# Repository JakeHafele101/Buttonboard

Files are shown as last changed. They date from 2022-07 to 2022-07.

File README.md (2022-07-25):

# Buttonboard Repository

Buttonboard takes button inputs from the drivers wheel and communicates those signals to HAL over our CAN network to turn on our lights and horn.

Some say this is the best board to ever exist on the team. Some also say that the smartest people on the team have worked on this board.

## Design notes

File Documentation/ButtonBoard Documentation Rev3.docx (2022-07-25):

Buttonboard

Project (P15) | Current Rev # C | March 18, 2021 | Bryce Staver

HARdware Documentation

Prisum solar car

2021

Revision History
Rev # | Description | Hardware Manager | Approved By Need 2/3 for approval: eteam director or assistant director, eteam manager, or alumni
P14 Rev | P14 buttonboard | Bryan Kalkhoff
Rev 1 | Reworked buttonboard from P14 and simplified it a ton. This was started as a new member project Fall 2020. Most of the changes were done here. | Bryce Staver | Bryan Kalkhoff, Ashley Robertson
Rev 2 | We changed the 12V connector to a Megafit and added a reverse polarity protection. | Bryce Staver | Bryan Kalkhoff, Ashley Robertson
Rev 3 | Added input debouncing and power filtering for 12V_Main coming into the board | Bryan Kalkhoff | Douglas Zuercher, Ashley Robertson

Additional Resources……………………………………………………………………………………...9

Prisum Contacts..………………………………………………………………………………………9

Other Contacts………………………………………………………………………………………10

# Theory of Operation

## Description

Buttonboard is used to take in inputs from the driver of the car and send them to our compute module. It has one 6 pin connector to take in all these inputs, which are the core of the board. Buttonboard is powered off 12V_Main.

## Board Placement

Buttonboard is placed on the inside of the car on the driver’s side. Specifically, it is on the front panel by the steering column. Refer to Figure 1 for a diagram in how the board and inputs will fit into the car. Buttonboard’s dimensions are 4.355 inches long and 3.341 inches wide. The mounting holes are offset 5.842mm in the y direction and offset 6.35mm in the x direction. The diameter of the mounting holes is 4.445mm. The block diagram below gives a general idea of how the board will fit into the front of the car. Figure 2 below demonstrates where the board is being placed behind the wheel and under the steering column.

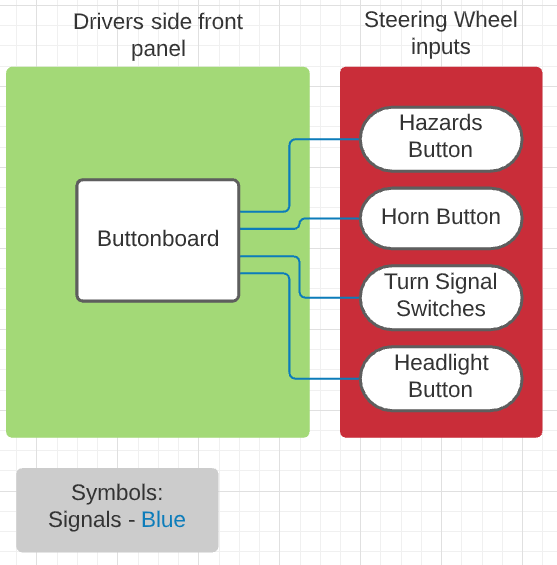
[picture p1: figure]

Figure 1. Buttonboard placement diagram

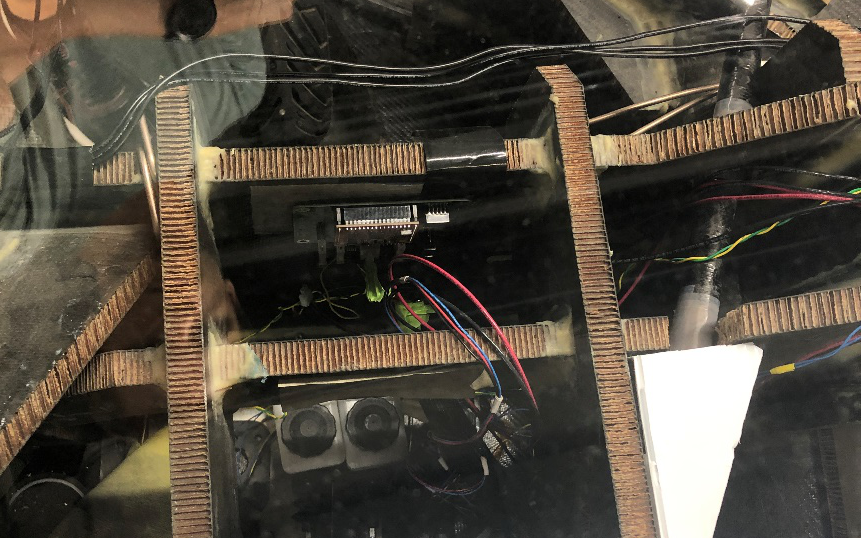
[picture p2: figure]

Figure 2. Buttonboard placement

## Purpose

the purpose of buttonboard is to provide an input driver interface for the car. The board will take in different inputs and send those signals to other boards through CAN to turn digital signals on or off for parts like our horn or turning lights.

# Application

## System Level

### Block Diagram

Buttonboard will get 12V_Main voltage from powerboard. The inputs in buttonboard will be processed through CAN and sent to front and rear HAL to turn on different signals in the car like turn lights, horn, or hazard lights. Figure 3 demonstrates a block diagram showing how buttonboard gets power from powerboard and sends its CAN signals to the front and rear HAL boards.

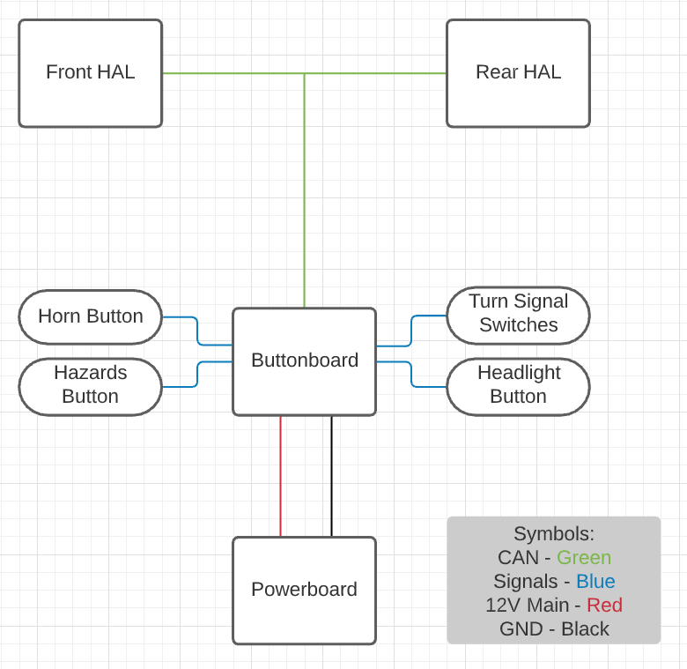
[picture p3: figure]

Figure 3. Buttonboard system diagram

### Pin Diagram

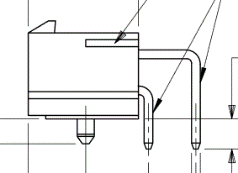
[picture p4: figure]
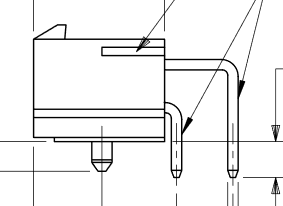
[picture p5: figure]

Figure 4. 2 pin connector diagram Figure 5. 6 pin diagram

A pin connection table is provided below for wiring purposes. In general, the wire with a greater voltage on it is connected to the lower pins, and the wire with a lower voltage on it is connected to the upper pins of a connector. The intention of wiring in this fashion is to decrease the chances of someone accidentally brushing the connector and touching the high-voltage signal.

Table 1: Pin diagram

Connector designator | Connector Type | Pin # | Description of Signal
J1 – 12V_Main | Megafit | 1 – MGND 2- 12V_Main | 12V_Main from powerboard
J2 – 5V_INPUT | Minifit | 1 – 5V 2 – MGND | 5V input possibly needed for buttons. NOT CURRENTLY USED
J3 – CAN1 | Minifit | 1 – CAN_H 2 – CAN_L | CAN1 Connector
J4 – CAN2 | Minifit | 1 – CAN_H 2 – CAN_L | CAN2 Connector
J5 – Button Inputs | Minifit | 1 – Left Turn 2 – Right Turn 3 – Horn 4 – Running Lights 5 – Hazards 6 - Brights | Takes in inputs for different buttons and switches from the driver’s side of car

To note here, right now we are not using both running lights and brights. When designing the board, we were unsure of if we would use both, so we have them labeled with different nets and inputs on connector J5. They are listed here since they are still a separate input in the schematic. It is now the case that Brights is being used now for cruise control, but that is not represented on the silkscreen on the board.

### Mounting buttons on wheels

There are 5 buttons attached on the driver’s wheel. The positive end of the buttons are wired through the J5 button input connector and the negative end of the button is wired through a chain of ground wires that go around the wheel. The buttons on the wheel are left turn, right turn, horn, hazards, and cruise control. Left turn, right turn, cruise control, and the hazards buttons are all latching. For the sake of everyone’s ears, the horn is non latching, so it will not stay pressed down after pushed.

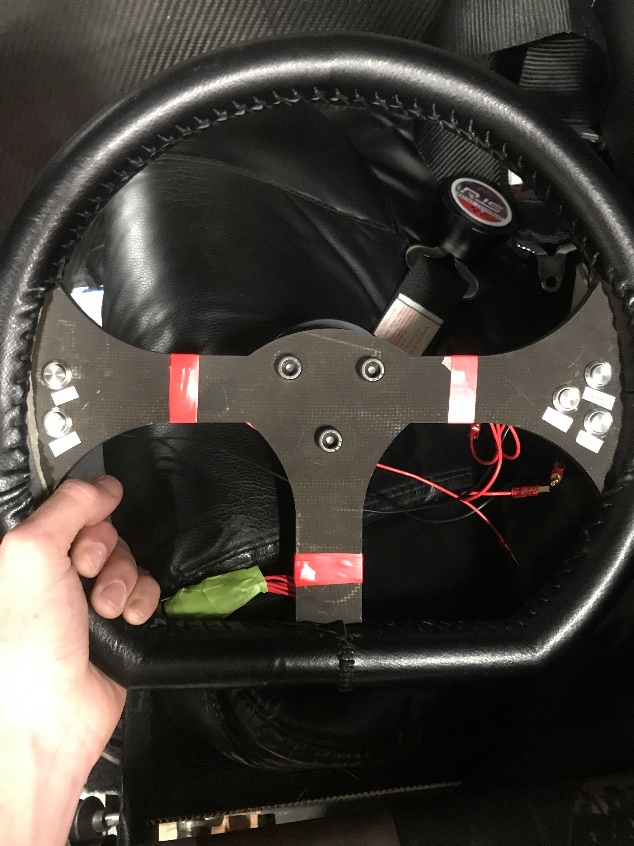
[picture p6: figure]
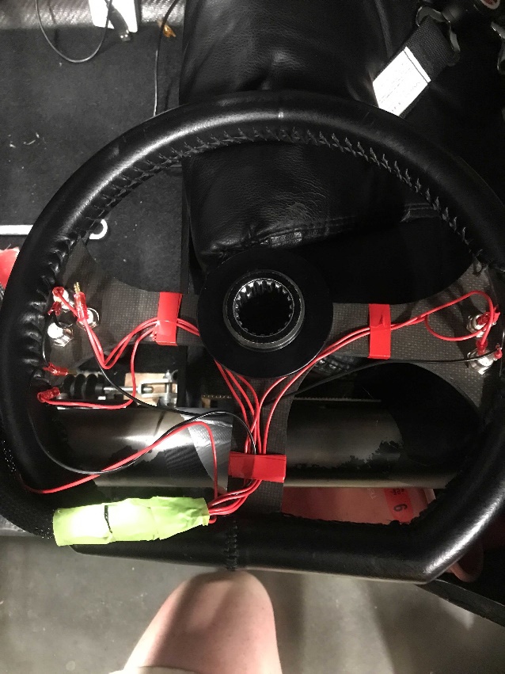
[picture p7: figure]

Figure 6. Back of wheel Figure 7. Front of wheel

## Board Level

### Schematic

Buttonboard’s schematic can be seen in Figure 10. For connectors, it should be noted that J1, the 12V_Main connector, is a megafit connector instead of a minifit, unlike the other connectors. This is something that was changed across all the boards to help us from accidentally frying compute modules.

Power

The circuitry between the 12V_Main megafit connector and the 5V switching reg, U1, is standard between a few different boards. Specifically, HAL and motorboard were designed around the same time as buttonboard and share a similar circuit and parts. The first PMOS, Q2, is used for reverse polarity protection. This is here so that just in case we accidentally swap our 12V and MGND inputs, we can’t accidentally burn anything up. Since we are using a PMOS, if our ground is connected in the right pin of the connector, pin 1, then the gate will enable the mosfet to send the 12V source from the drain (3 of Q2) to source (2 of Q2). F1 is our fuse holder. If our fuse is blown or not connected, a second PMOS (Q1) will turn on the Fault LED indicator. C1 is a decoupling capacitor that helps smooth out our input voltage into the 5V switching regulator. D1 is a TVS diode that helps to prevent fast voltage spikes to protect our circuit.

U1 is our switching regulator that turns our 12V voltage into 5V. Because of the TVS diode (D1), we had a 0.7V drop in our input, which LED us to use R1 and R3. These two resistors are used to adjust the output voltage to help us get as close to 5V as we can. Before we added these, we were getting around a 4.2 V output. After the switching regulator we have a 5V LED Indicator to show that the switching regulator is working as we need and to show that our 5V plane on top of the board has voltage on it.

The power filtering circuit, shown in Figure 8, helps us smooth high frequency noise from our 12V line coming into buttonboard. FB1 is a ferrite bead, which can be used to filter out the unwanted noise. The capacitors after it are designed to be placed in decreasing order of capacitance and size. If you look at the PCB design, you will notice that C1 and C8 have a package size of 1206, C9 has 0805, and C10 has 0603. They also decrease in order of capacitance, which is easier to see on the schematic.

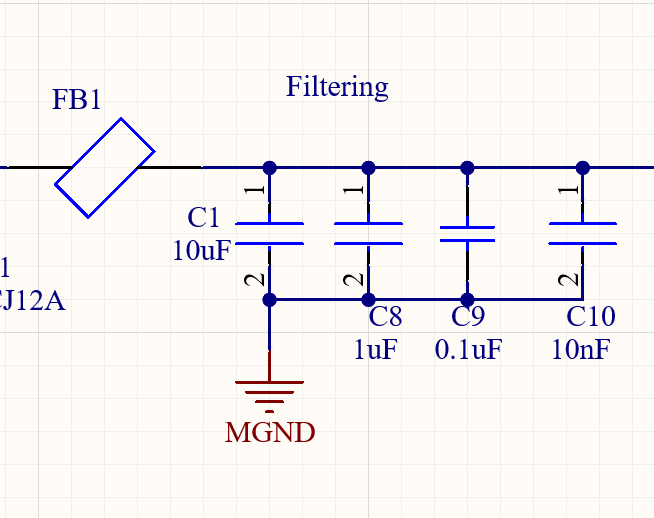
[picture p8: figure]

Figure 8. Power filtering circuit

Connectors

We have two connectors for can, which can be seen with the J3 and J4 connectors. These go into the CANH and CANL pins of the S+ (U2). For the input section, we have a 6 pin minifit connector, J5, used to get our actual button and switch inputs from the car. These inputs will then go into Port B pins of the S+.

Pullup Resistors

Each input is wired to a pullup resistor, as seen by R4 for example. This makes it so that all the inputs will default to a logic high normally. J2 as of now will not be used, but we kept it in as a 5V input just in case we needed it with the button inputs. This was added Fall 2020 and could possibly be changed for future revs.

Input Debouncing

Below, in Figure 9, is an example of an input debouncing circuit I created in falstad, an online circuit simulation app. On the left, between the 5V line and button, is our ordinary pull up resistor circuit we used in Rev2 and previous iterations. Normally the MCU input would go between the Button and leftmost 1k resistor, and detect the change between 5V and GND. But now, we use a resistor and capacitor to filter this circuit. When you press a button down, the voltage doesn’t smoothly jump to 5V, as it will “bounce”. To counter this, we include a capacitor to take the “noisy” voltage that is constantly jumping as the voltage gets pulled down on a button press. This works because current through a capacitor is C times the change in voltage. So, after the voltage is “smoothed out”, the change in voltage will be extremely low, so barely any current will flow through the capacitor once it is filtered, leaving the voltage to cleanly be read by the microcontroller input.

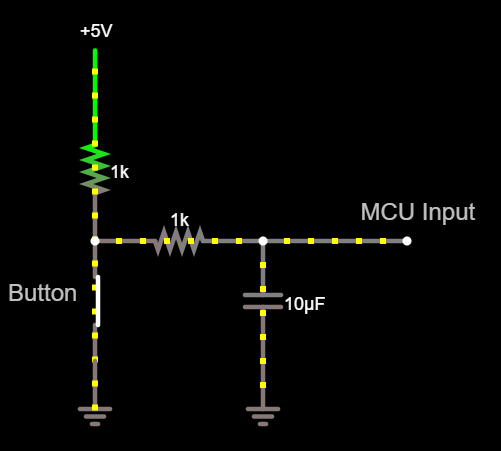
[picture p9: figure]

Figure 9. Input debouncing circuit

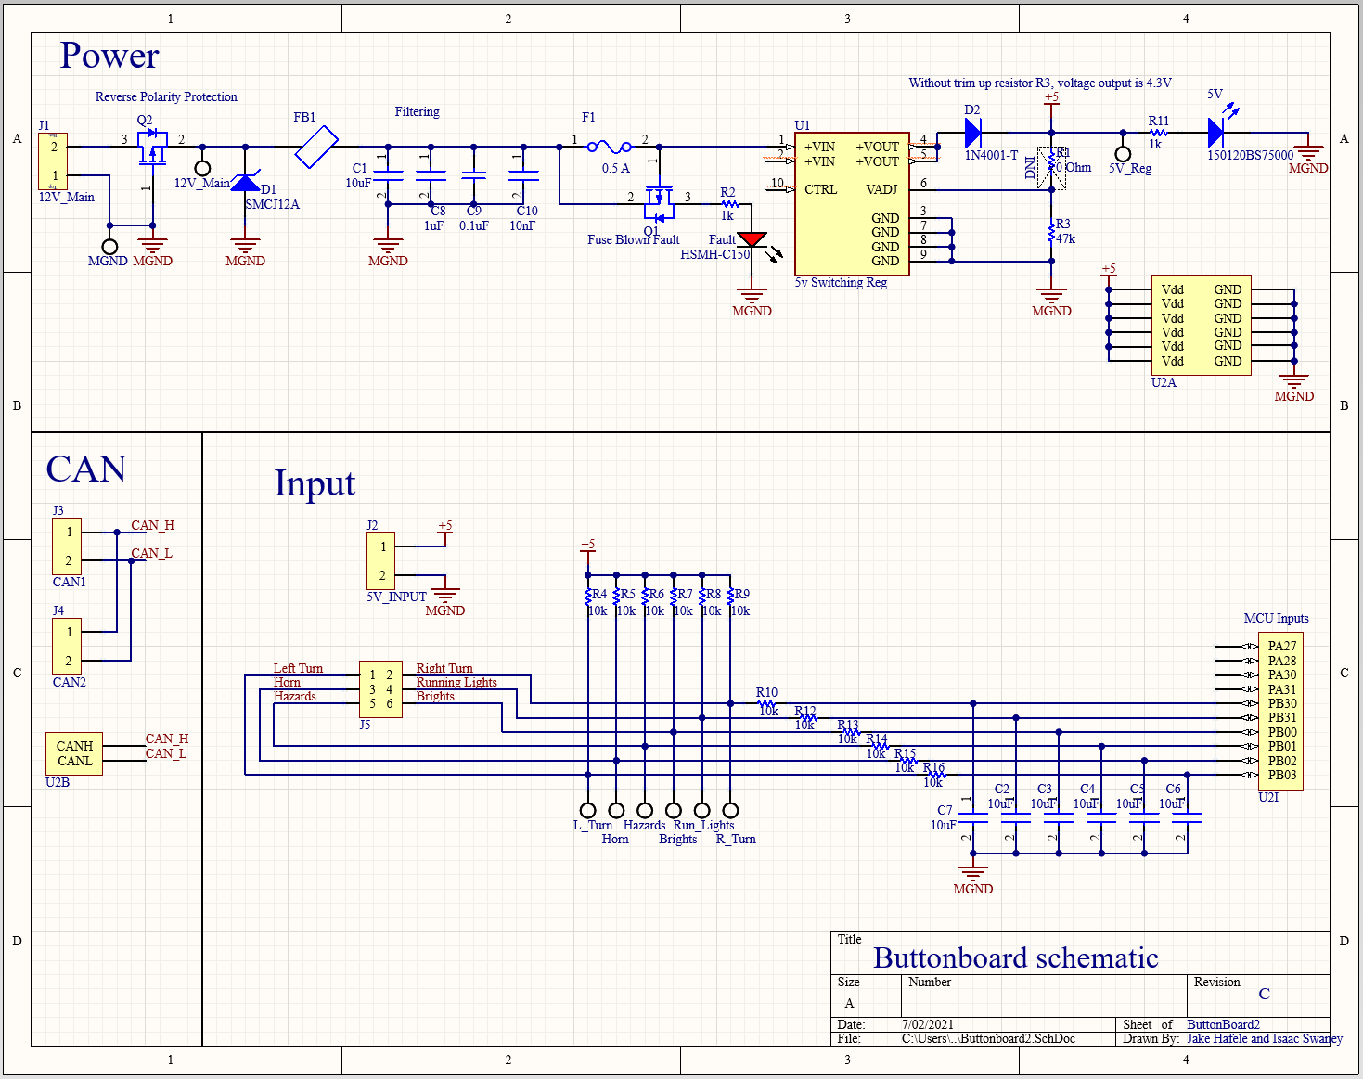
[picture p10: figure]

Figure 10. ButtonBoard.SchDoc

### PCB Picture

A picture of buttonboard’s PCB can be seen in Figure 11 below. The layout of the board is simple overall. On the left side of the board, we have our 12V_Main connector and all our power protection and switching regulator. All the components to the left of the compute module relate to the Power section of the schematic. To note with this, Figure 12 shows the 0.5 A silkscreen that is used to denote what type of fuse we need in the fuse holder. The CAN connectors are on the top right of the board, and the button inputs can be seen to the left of them on J5. We aligned all the pull up resistors in between this connector and the compute near the middle of the board. We also added test points for a couple different things. We added test points for MGND, 5V, and 12V_Main on the left side of the board so it is easy to see if our fuse and switching regulator are working as planned. We also added test points and labels for all our different inputs on the right of the board. We made it a point to include these on the sides of the board so they would be easy to probe and access. The only notable change of Rev3 was adding the fill for a small ground plane between C1 through C10. We placed three vias throughout to plane to make sure ground was evenly covered in it, but it made it very easy to ground the capacitors for filtering.

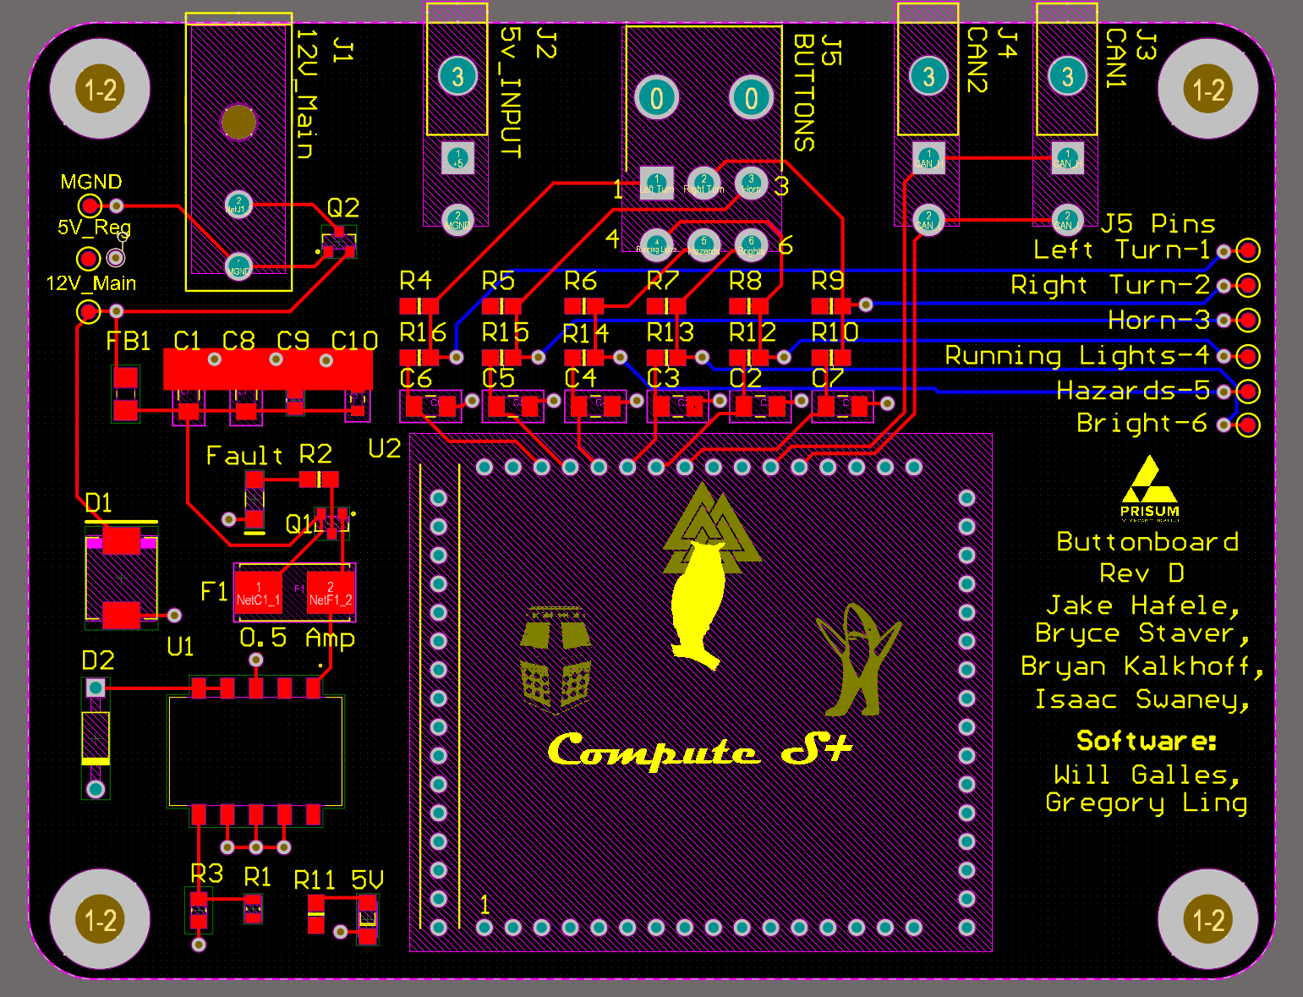
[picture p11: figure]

Figure 11. ButtonBoard.PcbDoc

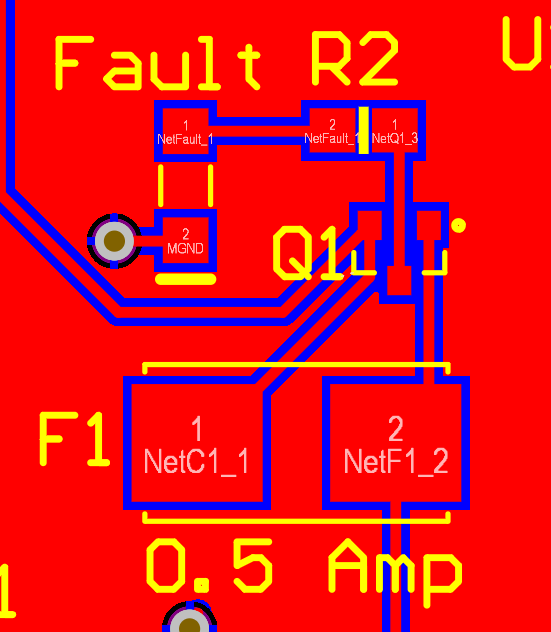
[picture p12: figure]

Figure 12. PCB Fuse and circuit protection block

### Project Specifics

Using Figure 13 we can find the correct trim up resistor to adjust the output voltage to match 5V. According to figure 14, if we include a diode before VOut we need to add that voltage drop onto Vo, which will be roughly 0.7V. After plugging in values of R1, R2, R3, Vo, and VRef for the values spec’d out at the 5V switching regulator, we get a trim up resistor of 47 kOhms. Based on the protection diagram in Figure 5, we do not need to include a trim down resistor, and only a trim up resistor. This is a mistake I made while testing during Rev B.

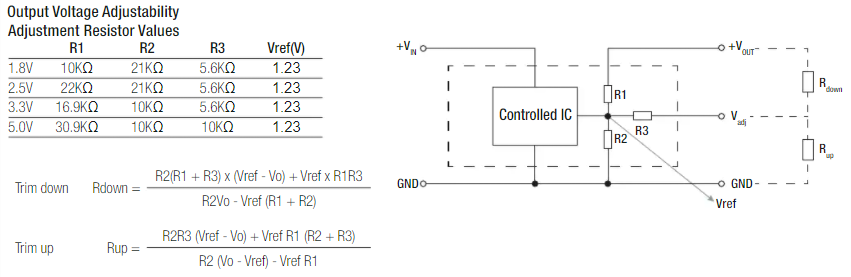
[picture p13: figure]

Figure 13. 5V Switching Regulator resistor equations

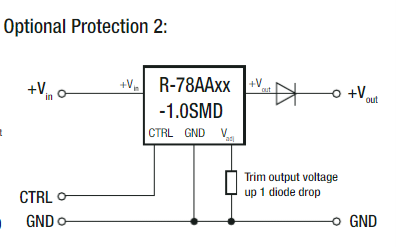
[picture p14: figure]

Figure 14. 5V Switching regulator diode protection

# Proof of Operation

## Test Procedure

Testing hardware for buttonboard Rev B and Rev C was very straightforward. Since Rev C only changed the 12V_Main connector, testing was the same for both revs. After soldering all our parts on, we tested for continuity by probing different parts of the board. More specifically, we tested for continuity around our fuse and switching regulator, to make sure we would get our 5V out. We also tested the board plugged in without a fuse to make sure the Fault indicator would light up. After this, we probed the test points of the inputs to make sure that they were default high signals normally. We then grounded the inputs to make sure that the test points and the input lines would change to a low or 0 signal. This was the extent of our testing for buttonboard so far, and it will almost definitely be the same process when we get our new board for Rev C soon.

For testing buttonboard in the future, follow this checklist:

1. Does the power LED indicator turn on after providing a 12V source in J1?
2. Does the 5V switching regulator output 5V? This can be checked by probing the 5V and MGND test points. If not, try checking you placed the trim up resistor on R3 and not R1!
3. Make sure ground is on the top pin of the connector (1) and the 12 V line is on the bottom (2). Refer to the 2 pin Minifit connector in the pin diagram above.
4. Test reverse polarity by swapping the 12V and ground line on J1 and make sure the board DOES NOT turn on (Thanks to Q2)
5. Test the fuse blown circuit by making sure the FAULT LED turns on when you take out a fuse cartridge (Thanks to Q1)
6. Make sure the button inputs (test points on the right) are all about 5V by default (this is because they are pull up resistors, they will be grounded to 0V when pressed)
7. Celebrate because you just aced the best god damn board on this car

## Test Results

The only thing that was wrong with hardware during testing was that our output voltage from the 5V switching regulator was around 4.2 V. After looking at the schematic, we determined that this was because of the TVS diode before the voltage output, which was dropping the voltage. To fix this, we set the output voltage to 5.7V to account for the diode drop and calculate the trim up resistor based on Figure 4 and Figure 5.

## Troubleshooting

If any step of the test procedure failed, follow the troubleshooting for that step below:

1. Check if the fuse blown LED is on from a blown fuse, and check if the power LED is soldered on the right way with a diode check
2. Make sure you have the trim up resistor on the right trim pad and that it is the right value
3. To confirm this, check which pin is connected to the bottom layer/plane of the board which is ground. The pin closer to the inside of the board should be grounded.
4. Verify an N-MOS is on Q2
5. Make sure the fuse is out and the fault LED is facing the right direction
6. Same as step 2

## Race Considerations

If either the 0.5 A fuse on F1 is blown or there is not a fuse in the fuse holder, the FAULT LED indicator will light up. This should never be on. Instead, the 5V LED indicator should be on if 12 volts goes through the switching regulator. Both are on the left side of the board and can be seen in the PCB in Figure 2. Only one should be on at once and should indicate the current condition of power through the board.

## Future Considerations

Standardizing parts between 2020’s new member projects were a big plus for buttonboard. When I was working on the schematic, it was helpful to share parts or circuit protection with other boards like HAL or motorboard. To note, many of the boards shared the same switching regulator and circuit protection, since these boards all had the same 12V input coming into them. This is something that makes life easier for people ordering parts and the people designing them. For future revisions of the board there might also be some worthwhile information in documentation from both HAL and motorboard.

Another small thing is to remember to buy fuses with your fuse holders. We forgot to do this for Rev B, since only the fuse holder was on our schematic. This is something currently in our BOM but could be forgotten easily if someone makes a fresh one for a change.

# Additional Resources

## PrISUm Contacts

Name | ISU Email | Personal Email | Phone
Jake Hafele | jmhafele@iastate.edu | jakehafele@gmail.com | (309)-696-0228
Bryan Kalkhoff | bryank@iastate.edu | bsk678@live.com | N/A

# Appendix

## Reference

5V Switching Regulator Datasheet (U1) - https://www.digikey.com/htmldatasheets/production/705190/0/0/1/r-78aa-1-0-series-datasheet.html

## Figures

Figure 1. Buttonboard placement diagram

Figure 2. Buttonboard placement

Figure 3. Buttonboard system diagram

Figure 4. 2 pin connector diagram

Figure 5. 6 pin diagram

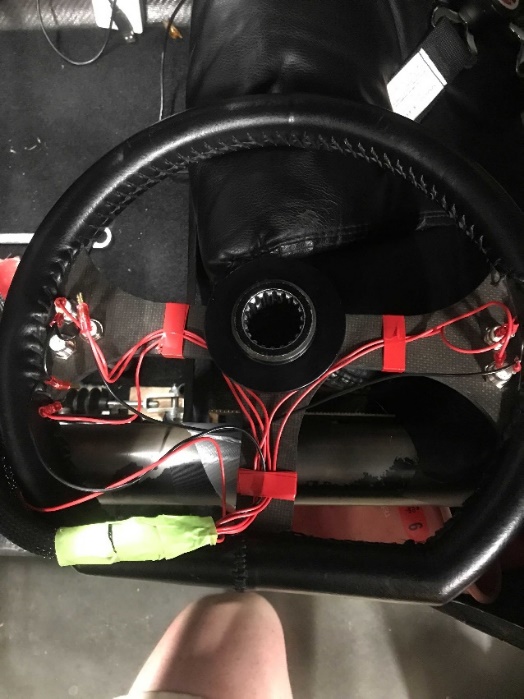
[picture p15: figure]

Figure 6. Back of wheel

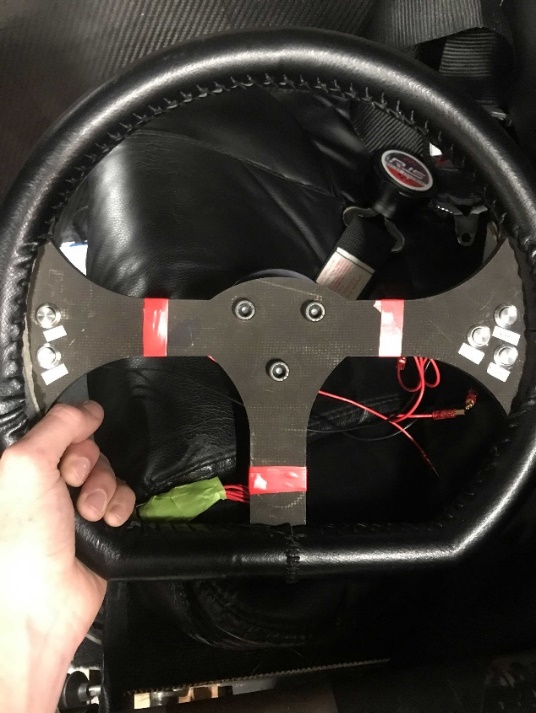
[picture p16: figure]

Figure 7. Front of wheel

Figure 8. Power filtering circuit

Figure 9. Input debouncing circuit

Figure 10. ButtonBoard.SchDoc

Figure 11. ButtonBoard.PcbDoc

Figure 12. PCB Fuse and circuit protection block

Figure 13. 5V Switching Regulator resistor equations

Figure 14. 5V Switching regulator diode protection

## BOM List

Item # | Amount per board | Designator | Manufacturer Number | General Part
1 | 1 | J1 | 768250002 | 2 Pin Megafit
2 | 3 | J2 J3 J4 | 39300020 | 2 Pin Minifit
3 | 1 | J5 | 39295063 | 6 Pin Minifit
4 | 2 | R2 R11 | CRG0805F1K0 | 1k Resistor
5 | 1 | R3 | CRGCQ0805F47K | 47k Resistor
6 | 12 | R4 R5 R6 R7 R8 R9 R10 R12 R13 R14 R15 R16 | RMCF0805FT10K0 | 10k Resistor
7 | 1 | 5V | 150120BS75000 | Blue LED
8 | 1 | Fault | HSMH-C150 | Red LED
9 | 1 | F1 | 01550900M | Fuse Holder
10 | 1 | F1 | 0451.500MRL | Fuse
11 | 1 | D1 | SMCJ12CA | Diode
12 | 1 | D2 | 1N4001-T | Diode
13 | 1 | U1 | PPPC161LFBN-RC | Compute Female headers
14 | 7 | C1 C2 C3 C4 C5 C6 C7 | CL31A106MOHNNNE | 10 uF capacitor
15 | 1 | C8 | 12065G105ZAT2A | 1 uF capacitor
16 | 1 | C9 | 08055C104JAT2A | .1 uF Capacitor
17 | 1 | C10 | C1608X7R1H103K080AA | .01 uF Capacitor
18 | 1 | FB1 | HI1206N800R-10 | Ferrite Bead
19 | 2 | Q1 Q2 | AO3419 | PMOS

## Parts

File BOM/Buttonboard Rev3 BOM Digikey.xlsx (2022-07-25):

General Part | CUST REF | PCB Label | Manufacturer Number | Digikey Number | Amount per board | Order Amount | Package | Value | Precision | Power
2 Pin Megafit | Buttonboard J1 | J1 | 768250002 | WM11969-ND | 1 | 5
2 Pin Minifit | Buttonboard J2 J3 J4 | J2 J3 J4 | 39300020 | WM21351-ND | 3 | 15
6 Pin Minifit | Buttonboard J5 | J5 | 39295063 | WM3922-ND | 1 | 5
1k Resistor | Buttonboard R2 R11 | R2 R11 | CRG0805F1K0 | A106056CT-ND | 2 | 10 | 805 | 1k | 1% | 1/8 W
47k Resistor | Buttonboard R3 | R3 | CRGCQ0805F47K | A129769CT-ND | 1 | 5 | 805 | 47k | 1% | 1/8 W
10k Resistor | Buttonboard R4 R5 R6 R7 R8 R9 R10 R12 R13 R14 R15 R16 | R4 R5 R6 R7 R8 R9 R10 R12 R13 R14 R15 R16 | RMCF0805FT10K0 | RMCF0805FT10K0CT-ND | 12 | 60 | 805 | 10k | 1% | 1/8 W
Blue LED | Buttonboard 5V | 5V | 150120BS75000 | 732-4989-1-ND | 1 | 5 | 1206
Red LED | Buttonboard Fault | Fault | HSMH-C150 | 516-1439-6-ND | 1 | 5
Fuse Holder | Buttonboard F1 | F1 | 01550900M | F1889-ND | 1 | 5
Fuse | Buttonboard F1 | F1 | 0451.500MRL | F2574CT-ND | 1 | 5 | 2-SMD | 0.5 A
Diode | Buttonboard D1 | D1 | SMCJ12CA | SMCJ12CALFCT-ND | 1 | 5
Diode | Buttonboard D2 | D2 | 1N4001-T | 1N4001DICT-ND | 1 | 5
Compute Female headers | Buttonboard U1 | U1 | PPPC161LFBN-RC | S7049-ND | 1 | 5
10 uF capacitor | Buttonboard C1 C2 C3 C4 C5 C6 C7 | C1 C2 C3 C4 C5 C6 C7 | CL31A106MOHNNNE | 1276-2877-1-ND | 7 | 35 | 1206
1 uF capacitor | Buttonboard C8 | C8 | 12065G105ZAT2A | 478-1580-1-ND | 1 | 5 | 1206
.1 uF Capacitor | Buttonboard C9 | C9 | 08055C104JAT2A | 478-3352-1-ND | 1 | 5 | 805
.01 uF Capacitor | Buttonboard C10 | C10 | C1608X7R1H103K080AA | 445-1311-1-ND | 1 | 5 | 603
Ferrite Bead | Buttonboard FB1 | FB1 | HI1206N800R-10 | 240-2409-1-ND | 1 | 5
PMOS | Buttonboard Q1 Q2 | Q1 Q2 | AO3419 | 785-1013-1-ND | 2 | 10
BOM for documentation:
Item # | Amount per board | Designator | Manufacturer Number | General Part
1 | 1 | J1 | 768250002 | 2 Pin Megafit
2 | 3 | J2 J3 J4 | 39300020 | 2 Pin Minifit
3 | 1 | J5 | 39295063 | 6 Pin Minifit
4 | 2 | R2 R11 | CRG0805F1K0 | 1k Resistor
5 | 1 | R3 | CRGCQ0805F47K | 47k Resistor
6 | 12 | R4 R5 R6 R7 R8 R9 R10 R12 R13 R14 R15 R16 | RMCF0805FT10K0 | 10k Resistor
7 | 1 | 5V | 150120BS75000 | Blue LED
8 | 1 | Fault | HSMH-C150 | Red LED
9 | 1 | F1 | 01550900M | Fuse Holder
10 | 1 | F1 | 0451.500MRL | Fuse
11 | 1 | D1 | SMCJ12CA | Diode
12 | 1 | D2 | 1N4001-T | Diode
13 | 1 | U1 | PPPC161LFBN-RC | Compute Female headers
14 | 7 | C1 C2 C3 C4 C5 C6 C7 | CL31A106MOHNNNE | 10 uF capacitor
15 | 1 | C8 | 12065G105ZAT2A | 1 uF capacitor
16 | 1 | C9 | 08055C104JAT2A | .1 uF Capacitor
17 | 1 | C10 | C1608X7R1H103K080AA | .01 uF Capacitor
18 | 1 | FB1 | HI1206N800R-10 | Ferrite Bead
19 | 2 | Q1 Q2 | AO3419 | PMOS
